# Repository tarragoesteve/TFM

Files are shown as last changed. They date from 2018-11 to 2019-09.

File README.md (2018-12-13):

# TFM
My final degree thesis is based on the construction and design of a compact remote controlled segway. Here you will find the software and the hardware needed to build one yourself when it's finished.

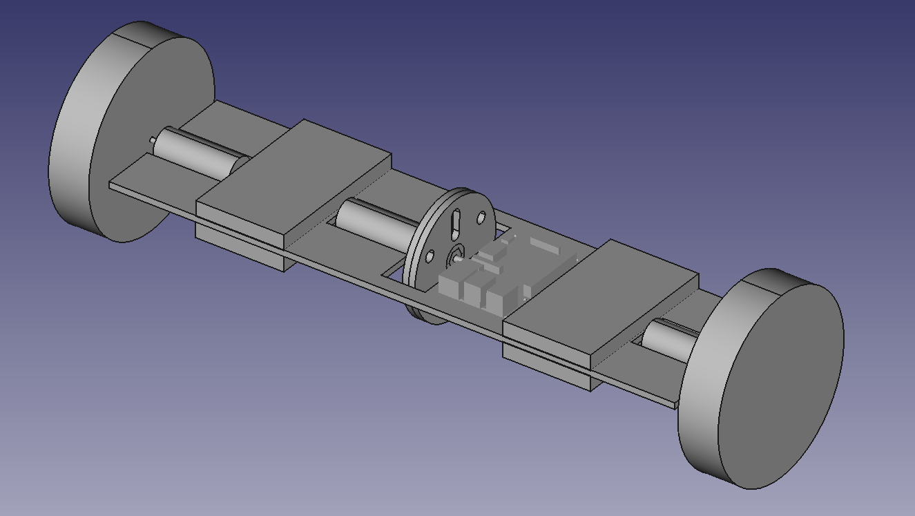
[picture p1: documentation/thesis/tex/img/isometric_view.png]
3D preview


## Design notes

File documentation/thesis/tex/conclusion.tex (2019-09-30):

\section{Conclusion}
Thinking, designing and building a prototype is a big and rewarding challenge.
There are many things that do not work as expected and you need to iterate again
and find a solution to the problem. Some examples are too much deformation in the platform,
too noisy speed measurements or 3D printed parts that we couldn't unpack.

You may see a gallery of photos
of the process in this \href{https://photos.app.goo.gl/dJozKgFnNSdTapSy6}{link} (\href{https://photos.app.goo.gl/dJozKgFnNSdTapSy6}{https://photos.app.goo.gl/dJozKgFnNSdTapSy6}).

On the other hand we came out with a model using the fundamental mechanics equations, but we are missing
some frictions and other forces that do not appear in our model. This made our robot behave a little bit
different from expected from simulations. With the flywheel mode the robot can hardly start moving and with
the pendulum mode the platform needs to turn a little to start and brake.

For a possible following iteration I would recommend much more powerful motors and a more robust structure.
The robot now is not behaving perfectly but can move around more or less as expected, as you can see in this
\href{https://youtu.be/yWOlyIL4cP0}{video} (\href{https://youtu.be/yWOlyIL4cP0}{https://youtu.be/yWOlyIL4cP0}).

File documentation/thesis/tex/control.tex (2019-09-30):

\section{Control}
So far we have analyzed our system as a continuous system.
However, we are using the Raspberry Pi to control the robot, so we will
be using digital control. It's a branch of control theory that uses
digital computers to act as system controllers.

In order to sample the position and the speed we use the rotatory encoders.
They count the number of flags so there is a constant to convert them into radians.

All our digital control was made in periodical loops. To get the speed we
divided the incremental position by the period of the loop. All the controllers
are PID controllers, each of time with different inputs, constants and outputs.

A PID controller continuously calculates an error value $e(t)$ as the difference between
a desired set point and a measured process variable and applies a
correction based on proportional, integral, and derivative terms
(denoted $K_p$, $K_i$, and $K_d$ respectively).

To adjust the controller constants in all cases we used the Ziegler-Nichols method:
\footnote{Ziegler, J.G \& Nichols, N. B. (1942). "Optimum settings for automatic controllers".
 Transactions of the ASME. 64: 759-768.}

\begin{enumerate}
    \item Set all gains to zero.
    \item Increase the $K_p$ gain until the response to a disturbance is steady oscillation.
    \item Increase the $K_d$ gain until the oscillations go away (i.e. it's critically damped).
    \item Repeat steps 2 and 3 until increasing the D gain does not stop the oscillations.
    \item Set $K_p$ and $K_d$ to the last stable values.
    \item Increase the $K_i$ gain until it brings you to the set point with no oscillations desired.
\end{enumerate}

\subsection{Position control}
The input variable is the angle we would like the motor to achieve. We sense that angle
with our rotatory encoder. The output is a PWM signal and the direction the motor has to move.

The first steep was to control the position of a peg attached to the motor.
This allowed us to move the rotor from outside and also check and adjust our encoder.
In figure \ref{fig: control peg} you can see a picture of the set up we had.

\begin{figure}[H]
    \centering
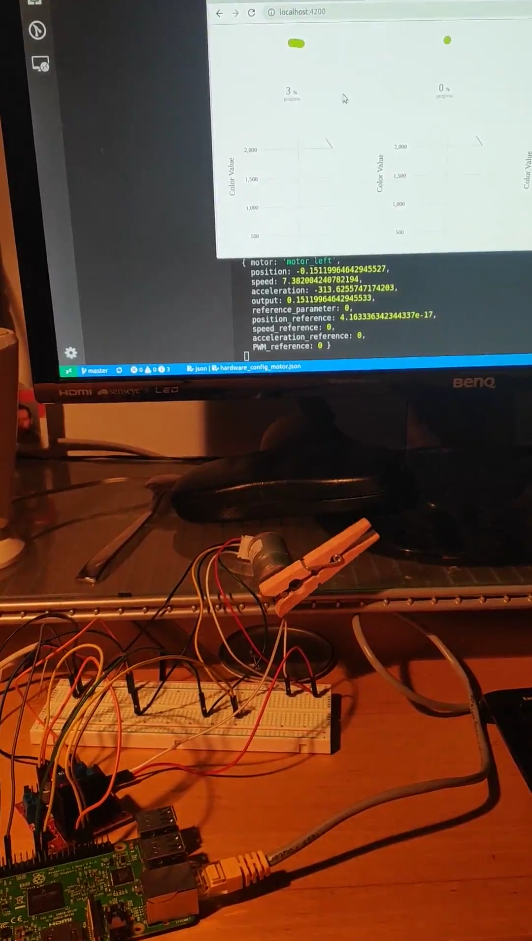
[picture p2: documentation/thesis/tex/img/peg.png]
    
    \caption{Picture of the set up to control the peg.}
    \label{fig: control peg}
\end{figure}

Once knowing the constants that worked well for our peg,
we proceed the same method with the flywheel position but having a
starting point from the peg experiment.

\subsection{Speed control}
The input variable is the desired speed. We get the real speed by dividing the incremental angle
by the period (50 ms). This leaded to noisy measurements, so we decided to apply an average filter (3 samples) to
the result.

We use the motor speed control to be able to control the direction in which the robot is moving.
We transform a two-axis joystick signal (x,y) into speed set points for the PID of the wheels
 with the following formula:
\begin{equation}
    \begin{split}
    Speed_{right} = x + y \\
    Speed_{left} = x - y    
    \end{split}
\end{equation}
\subsection{Inclination control}
In order to control the inclination of the platform we also used a PID controller.
We sense the inclination of the platform with the accelerometer, and then we compute the error
as the difference between desired inclination and sensed inclination. Them, the we feed the 

\begin{itemize}
    \item In the flywheel case we simply output this error to the flywheel PWM motor signal.
    \item In the pendulum case this output is mapped to domain from -90 degrees to 90 degrees.
    Then this signal feeds another PID controller to control the position of the pendulum. We know
    the position of the pendulum by adding the inclination we sense to the rotation of the flywheel motor.
\end{itemize}

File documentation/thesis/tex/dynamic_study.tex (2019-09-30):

\section{Rectilinear movement dynamics with $r_{flywheel}$ fixed}
This section studies the dynamics of the robot and the transition between states
to answer questions as how fast can we reach the maximum speed or how quickly can we
accelerate during a concrete period.

In order to study the dynamics of the robot we will use Lagrange mechanics.
To reduce the number of variables we will study the case of rectilinear
movement by imposing that both wheels turn at the same speed. We will also set
the radius of the free weight to $r_{flywheel}$. Note that in this analysis the
platform is not assumed to keep a fixed inclination as before, but it is allowed to rotate.

The generalized coordinates ($q$) will be:
\begin{enumerate}
	\item $\phi_{ground-wheel}$: rotation of the wheel respect the ground.
	\item $\phi_{wheel-platform}$: rotation of the platform respect the wheel.
	\item $\phi_{platform-flywheel}$: rotation of the flywheel respect the platform.
\end{enumerate}

We will use two auxiliary variables:
\begin{enumerate}
	\item $\phi_{ground-platform}=\phi_{ground-wheel}+\phi_{wheel-platform}$: rotation of the platform respect the ground.
	\item $\phi_{ground-flywheel}=\phi_{ground-platform}+\phi_{platform-flywheel}$: rotation of the flywheel respect the ground.
\end{enumerate}

The total potential energy:
\begin{equation}
	V = m_{cylinder}\cdot (r_{flywheel}-r_{flywheel-max}) \cdot cos(\phi_{ground-flywheel}) \cdot g
\end{equation}
The total kinetic energy:
\begin{equation}
	T = \frac{1}{2}\cdot[\dot{\phi}_{ground-wheel}^2\cdot I_{wheel}
		+ \dot{\phi}_{ground-platform}^2 \cdot I_{platform}
		+ \dot{\phi}_{ground-flywheel}^2\cdot I_{flywheel}
		+ \dot{\phi}_{ground-wheel}^2\cdot r_{wheel}^2\cdot m_{total}]
\end{equation}
The Lagrangian is defined as:
\begin{equation}
	L=T-V
\end{equation}
Lagrange's equation is:
\begin{equation}
	\frac{d}{dt}(\frac{\partial L}{\partial \dot{q}_j})=
	\frac{\partial L}{\partial q_j}	+ F_{j}
\end{equation}
So in our case:
\begin{equation}
	\frac{\partial L}{\partial \dot{\phi}_{ground-wheel}}=
	\dot{\phi}_{ground-wheel} \cdot I_{wheel}
	+ \dot{\phi}_{ground-platform} \cdot I_{platform}
	+ \dot{\phi}_{ground-flywheel}\cdot I_{flywheel}
	+ \dot{\phi}_{ground-wheel}\cdot r_{wheel}^2\cdot m_{total}
\end{equation}
\begin{equation}
	\frac{\partial L}{\partial \dot{\phi}_{wheel-platform}}=
	\dot{\phi}_{ground-platform} \cdot I_{platform}
	+ \dot{\phi}_{ground-flywheel}\cdot I_{flywheel}
\end{equation}
\begin{equation}
	\frac{\partial L}{\partial \dot{\phi}_{platform-flywheel}}=
	\dot{\phi}_{ground-flywheel}\cdot I_{flywheel}
\end{equation}
We define M as the following matrix:
\begin{equation}
	\begin{pmatrix}
		I_{wheel} + I_{platform} + I_{flywheel} + r_{wheel}^2 \cdot m_{total} &
		I_{platform} + I_{flywheel}                                           &
		I_{flywheel}                                                            \\
		I_{platform} + I_{flywheel}                                           &
		I_{platform} + I_{flywheel}                                           &
		I_{flywheel}                                                            \\
		I_{flywheel}                                                          &
		I_{flywheel}                                                          &
		I_{flywheel}                                                            \\
	\end{pmatrix}
\end{equation}
In matrix form and with our generalized coordinates:
\begin{equation}
	\frac{\partial L}{\partial \dot{q}} =
	M \cdot \dot{q}
\end{equation}
\begin{equation}
	\frac{d}{dt}(\frac{\partial L}{\partial \dot{q}}) = 	M \cdot \ddot{q}
\end{equation}
Let $a$ be a constant:
\begin{equation}
	a = m_{cylinder}\cdot (r_{flywheel}-r_{flywheel-max}) \cdot g
\end{equation}
\begin{equation}
	\frac{\partial L}{\partial q} = a \cdot sin(\phi_{ground-flywheel}) \cdot
	\begin{pmatrix}
		1 \\ 1 \\ 1
	\end{pmatrix}
\end{equation}
So using Lagrange's equation we get:
\begin{equation}
	\boxed{
		M \cdot \ddot{q} = a \cdot sin(\phi_{ground-flywheel}) \cdot
		\begin{pmatrix}
			1 \\ 1 \\ 1
		\end{pmatrix} + F
	}
\end{equation}
\subsection{Simulations}
In this subsection we study different policies for the generalized forces
($F$) applied to the robot in rectilinear movement case.

The robot has 2 actuators, the motors between the wheel and the platform
and the motor between the flywheel and the platform.
All motors in the systems  have a limited torque related with the
speed as you may see in Figure \ref{fig: Motor torque}.

\begin{equation}
	\boxed{
		F =
		\begin{pmatrix}
			0 \\ \tau_{wheel-platform} \\ \tau_{platform-flywheel}
		\end{pmatrix}
	}
\end{equation}

In order to compare the different policies we compare their efficiency in performing the same task:
The robot must travel 30 radians (3 meters) and stop at the end. All the parameters from 
the simulation are set equal to the values found in section \ref{sec: parameters results}.
Keep in mind that the wheel radius is 10 cm.

Here you can see a table that summarize the results:
\begin{center}
	\begin{tabular}{ |c|c|c|c|c|c|c| } 
	 \hline
	 \textbf{Experiment} & \textbf{Total time(s)} & \textbf{Time to max speed(s)} 
	 & \textbf{Max speed(rad/s)} & \textbf{Time to brake(s)}\\
	 \hline
	 \textbf{Controlling inclination} \\
	 \hline
	 Flywheel & 12,45 & 0,7 & 2,45 & 0,15\\
	 \hline
	 Pendulum & 5,59 & 2,69 & 10,36 & 2,90\\
	 \hline
	 Waitress & 8,24 & 4,12 & 5,49 & 4,12\\
	 \hline
	 \textbf{Free inclination} \\
	 \hline
	 Double flywheel & 3,9 & 1 & 8,51 & 0.27\\
	 \hline
	 Compose mechanism & 3,82 & 2,3 & 10,2 & 2,04\\
	 \hline
	\end{tabular}
\end{center}

\subsubsection{Controlling the platform inclination}
In the first two experiments we want to keep the platform in a horizontal position.
That's the reason why we force the $ \tau_{wheel-platform}$ equal to
$\tau_{platform-flywheel}$ in the experiments flywheel and pendulum.

\begin{enumerate}
	\item Flywheel
	
		The movable weight is fixed at $r_{max}$. In this experiment we consign the platform-flywheel motor to 
		output the maximum possible torque. Then the platform-wheels motors deliver
		the same torque. The platform-flywheel motor reaches in less than one second
		the maximum speed. This then limits the wheel-platform speed because no
		more torque can be applied one that point is reached.
	      \begin{figure}[H]
		      \centering
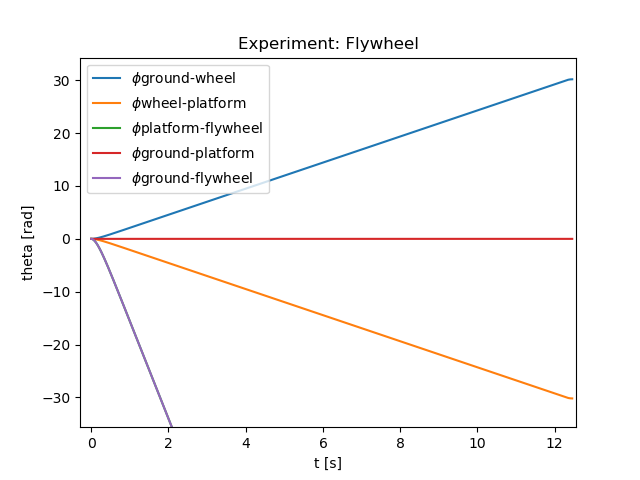
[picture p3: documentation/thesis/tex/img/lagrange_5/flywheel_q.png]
		      
		      \caption{Plot of the angles for the flywheel experiment.}
		      \label{fig:Simulation flywheel q}
	      \end{figure}

	      \begin{figure}[H]
		      \centering
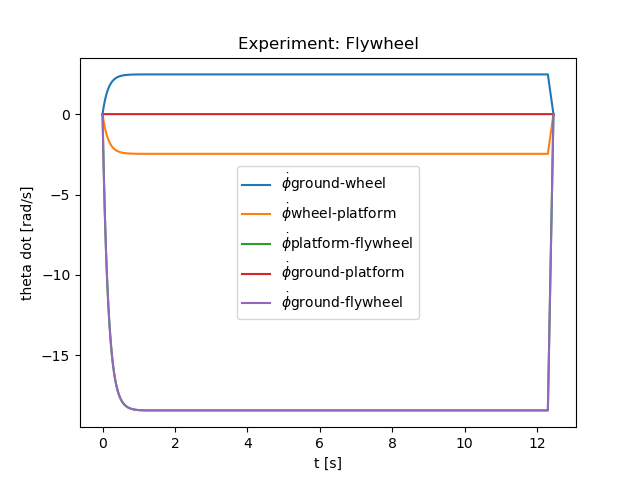
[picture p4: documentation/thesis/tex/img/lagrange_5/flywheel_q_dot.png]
		      
		      \caption{Plot of the angular velocities for the flywheel experiment.}
		      \label{fig:Simulation flywheel q dot}
	      \end{figure}
	\item Pendulum
	
		The movable weight is fixed at $r_{min}$. In this experiment we consign the platform-flywheel motor to 
		get to 90º with a PID controller. Then the platform-wheels motors deliver
		the same torque. The robot does not accelerate as fast as in the flywheel
		experiment but reaches a higher speed that allows it to travel the distance
		in less time. Note that the robot could have kept accelerating but had to
		brake before reaching the maximum speed. 
	      \
	      \begin{figure}[H]
		      \centering
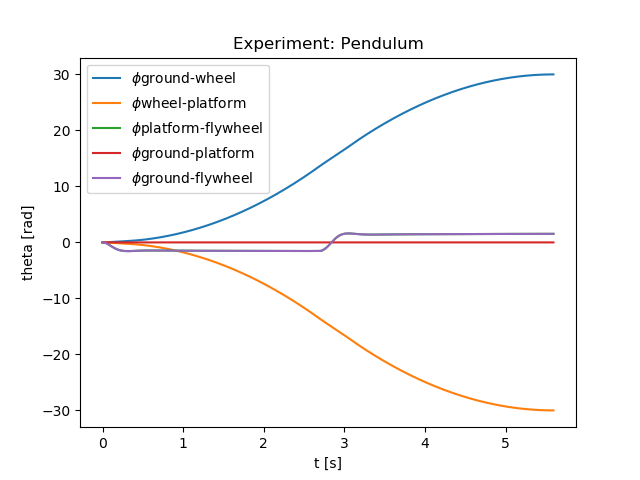
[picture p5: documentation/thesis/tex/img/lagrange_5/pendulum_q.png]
		      
		      \caption{Plot of the angles for the pendulum experiment.}
		      \label{fig:Simulation pendulum q}
	      \end{figure}

	      \begin{figure}[H]
		      \centering
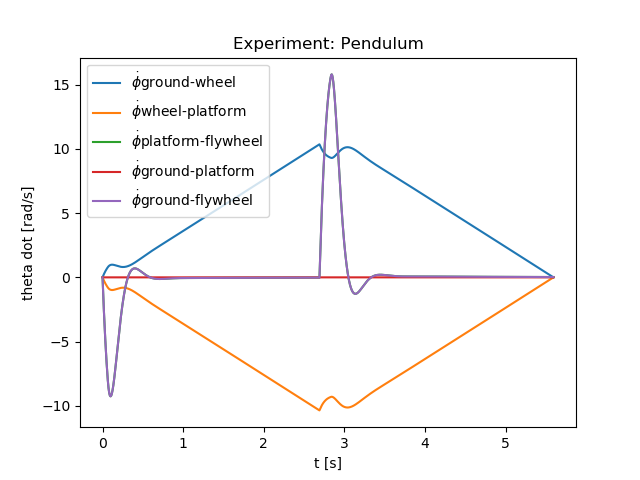
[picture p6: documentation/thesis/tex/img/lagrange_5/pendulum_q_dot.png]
		      
		      \caption{Plot of the angular velocities for the pendulum experiment.}
		      \label{fig:Simulation pendulum q dot}
	      \end{figure}
	\item Waitress
	
	The movable weight is fixed at $r_{min}$. This experiment is different from the previous two and its
	aim is to illustrate
		  how the robot could follow and inclination consign. The experiment is designed
		  the following way. A set point torque is given to the wheel-platform and the
		  flywheel-motor PID has an inclination consign too. The inclination consign is such
		  that the sum of accelerations received from and object in the platform is perpendicular
		  to the platform. 

	      \begin{figure}[H]
		      \centering
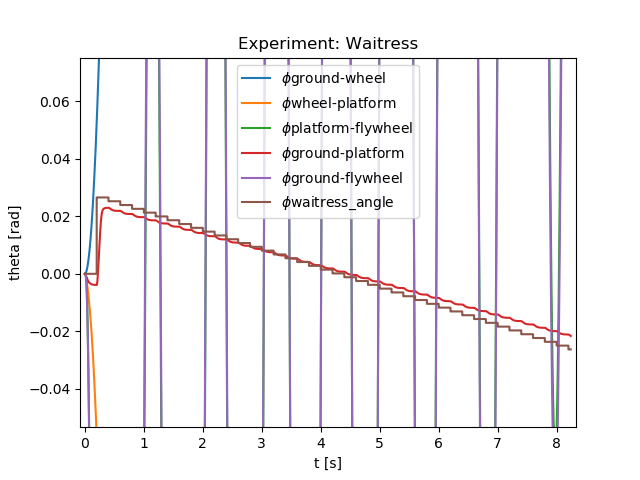
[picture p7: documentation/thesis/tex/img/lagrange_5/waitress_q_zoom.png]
		      
		      \caption{Plot of the angles for the waitress experiment.}
		      \label{fig:Simulation pendulum q}
	      \end{figure}

	      \begin{figure}[H]
		      \centering
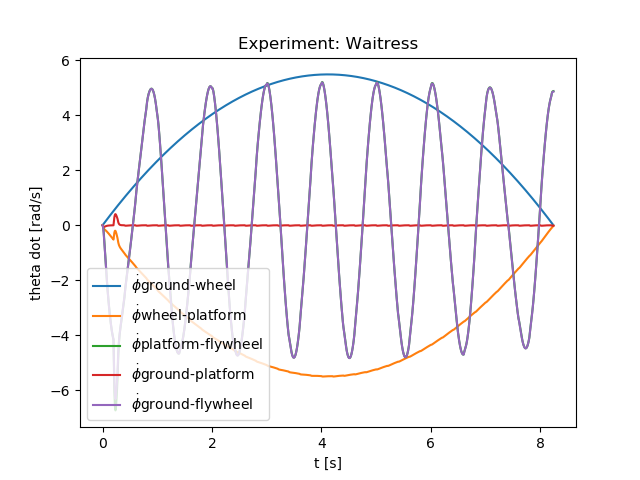
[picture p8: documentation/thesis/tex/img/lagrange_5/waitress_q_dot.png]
		      
		      \caption{Plot of the angular velocities for the waitress experiment.}
		      \label{fig:Simulation pendulum q dot}
	      \end{figure}

\end{enumerate}
\subsubsection{Letting the platform turn}
In this experiment we take advantage of the fact that the platform may not be needed
to stay horizontal in some displacement. The robot uses the platform as an
additional flywheel to help the robot accelerate and brake.
\begin{enumerate}
	\item Double Flywheel
	
	The movable weight is fixed at $r_{max}$. In this experiment we add the flywheel turn over the platform turn to 
		create more torque to accelerate our wheels. We always do the maximum possible torque with all the motors.
	      \begin{figure}[H]
		      \centering
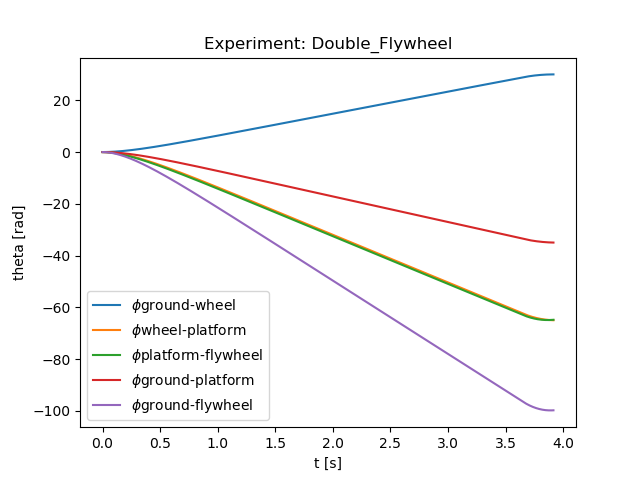
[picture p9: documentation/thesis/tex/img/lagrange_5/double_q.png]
		      
		      \caption{Plot of the angles for the double flywheel experiment.}
		      \label{fig:Simulation double q}
	      \end{figure}

	      \begin{figure}[H]
		      \centering
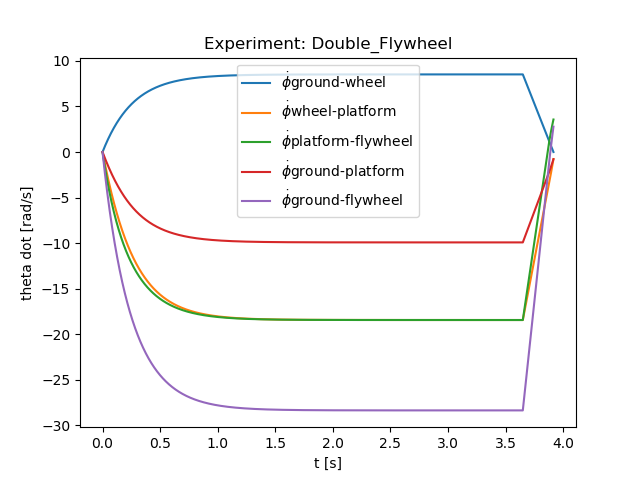
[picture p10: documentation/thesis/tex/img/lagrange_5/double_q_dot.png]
		      
		      \caption{Plot of the angular velocities for the double flywheel experiment.}
		      \label{fig:Simulation double q dot}
	      \end{figure}
	\item Compose
		  
	The movable weight is fixed at $r_{min}$. In this experiment we add the pendulum effect to the flywheel effect produced
		  by the flywheel. We do so with a PID controller for the angle ground-flywheel and making the maximum possible torque
		  with the platform-wheel motors. 
	      \begin{figure}[H]
		      \centering
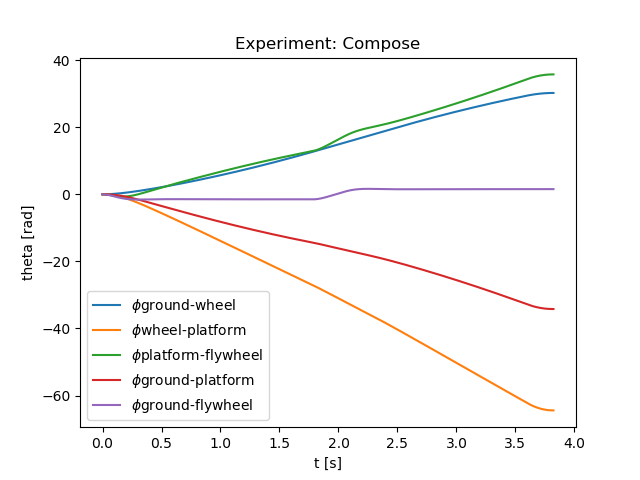
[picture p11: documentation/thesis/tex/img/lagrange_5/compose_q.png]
		      
		      \caption{Plot of the angles for the compose experiment.}
		      \label{fig:Simulation compose q}
	      \end{figure}

	      \begin{figure}[H]
		      \centering
		      
		      \caption{Plot of the angular velocities for the pendulum experiment.}
		      \label{fig:Simulation compose q dot}
	      \end{figure}
\end{enumerate}

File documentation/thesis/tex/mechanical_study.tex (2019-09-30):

\section{Mechanical analysis} \label{sec: mechanical analysis}
Once we know what we want to optimize, we need to know which is the relation with the design parameters.
In this section we will analyze and understand the key dynamics of our robot, so we can choose
the design parameters based on performance indicators. All the analysis is made
supposing the inclination of the platform is maintained fixed. As parameters, we have the width of the
flywheel masses $w$, the number of masses $N$, the radius of the flywheel $r_{flywheel}$, and
the radius of the wheels $r_{wheel}$.

\subsection{Inclination control}
In order to keep the inclination of the platform at a certain angle $\phi$ 
we must be able to compensate all the torque being applied to the platform.

\[\ddot{\phi}\cdot I_{platform} = \tau_{platform} \]

Assuming that the platform is well-balanced (the center of masses is located
at the rotation axis by our design restriction) and neglecting the torque generated
by the friction
with air, the sum of all the torques in the motor axis applied to the platform
is equal to the sum of the torque applied by the motors:

\[\tau_{platform} = \sum \tau_{motors}\]

The torque that the motors deliver to the wheels and to the flywheel create
a reaction in the platform in the opposite direction.

\[\tau_{platform} = -\tau_{motor-right-wheel} -\tau_{motor-left-wheel} -\tau_{motor-flywheel} \]

If we want keep the inclination $\phi$, we must be able to cancel $\tau_{platform}$.
Observe that the angular acceleration $\ddot{\phi}$ of the platform is linearly 
dependent with the torque it receives. 
\begin{equation} \label{eq:control equation}
\begin{split}
0 = -\tau_{motor-right-wheel} -\tau_{motor-left-wheel} -\tau_{motor-flywheel} \Rightarrow \\
\tau_{motor-right-wheel} +\tau_{motor-left-wheel} = -\tau_{motor-flywheel}
\end{split}
\end{equation}
In other words, we must overpass the torque of the wheels with the torque of the flywheel
if we want to control the inclination.

\subsection{Wheels torque}
The wheel torque we can induce is limited by the motor specifications.
Note that the maximum torque of the motor is a function of velocity and in particular 
at max speed the torque is zero. See figure \ref{fig: Motor torque} to see the plot of this function.

\[\tau_{motor-wheel} (\omega_{wheel}) \]

\begin{figure}
	\centering
    \begin{tikzpicture}
        %Axis
            \draw[->,thin] (center.center) -- (0,3.5) node[above] {$\tau_{motor}$};
            \draw[->,thin] (center.center) -- (3.5,0) node[right] {$\omega$};
        %Function
            \node (stall) at (0,3) [left]{stall torque};
            \node (maximum) at (3,0) [below]{maximum speed};
            \draw[-] (0,3) -- (3,0);
        \end{tikzpicture}
    \caption{Motor torque.}
	\label{fig: Motor torque}
\end{figure}

We assume that the wheels just roll and do no slip.
The robot is pushed by the wheels that make a force $F_{friction}$ against the ground in the contact point. See figure \ref{fig:Wheel force diagram}.

We can express the torque at the center of the wheel as:
\[\tau_{motor-wheel} + F_{friction} \cdot r_{wheel} = I_{wheel} 
\cdot \dot{\omega}_{wheel} \]
\begin{equation} \label{wheel torque equation}
\tau_{motor-wheel} = I_{wheel} \cdot \dot{w}_{wheel} - F_{friction} \cdot r_{wheel}
\end{equation}
\begin{figure}[ht]
	\centering
	\begin{tikzpicture}
        \path[rotate=30] node (center) at (2,2) {};
        \draw (center) circle (2);
        \draw[rotate=30] (0,0) -- (4,0);
        \draw[dashed] (0,0) -- (4,0);
        \path node[above] (right) at ([shift=({2,0})]center) {};
        \draw[<->] (center.center) -- (right.center)  node[below, midway] {$r_{wheel}$};;
    %Arcs
        \draw[rotate=30, ->] (4.5,2) arc (0:30:2.5) node[above]{$\omega_{wheel}$};
        \draw[rotate=30, ->, thick] (2.5,2) arc (0:60:.5) node[above]{$\tau_{motor-wheel}$};

        \draw[->] (1,0) arc (0:30:1) node[right]{$\alpha$};
    %Forces
        \draw[rotate=30,->,thick] (2,0) -- (3.5,0) node[above]{$F_{friction}$};
        \draw[rotate=30,->,thick] (2,0) -- (2,1) node[above]{$N$};
        \path node[above] (below) at ([shift=({0,-1})]center) {};
    
        \draw[->,thick] (center.center) -- (below.center) node[below]{$m\cdot g$};
        \draw[rotate=30,->,thick] (center.center) -- (1,2) node[below]{$F_{platform}$};
    \end{tikzpicture}
	\caption{Wheel force diagram.}
	\label{fig:Wheel force diagram}
\end{figure}

\subsection{Flywheel torque}
\begin{figure}
	\centering
    \begin{tikzpicture}
        %Circle
            \path node (center) at (0,0) {};
            \draw (center) circle (3);
        %Arcs
            \draw[->] (0,3.5) arc (90:120:3.5) node[above, midway]{$\theta$};
        %Movable mass
            \draw[rotate=120,fill=gray] (1.5,0) circle (.9) node (moving) [draw,circle]{};
        %Guide
            \draw[dashed,rotate=120] (.9,0) -- (2.1,0);
        %Other masses
            \foreach \i in {2}
            {
                \draw[rotate=60-60* \i,fill=gray] (3-.9,0) circle (.9) node[draw,circle]{};
            }
        %Radius
            \draw[<->] (0,0) -- (moving.center) node[near end, below] {$r$};
            \draw[rotate=-60,<->] (0,0) -- (2.1,0) node[midway, above] {$r_{max}$};
        %Axis
            \draw[->,thin] (center.center) -- (0,3.5) node[above] {$z$};
            \draw[->,thin] (center.center) -- (3.5,0) node[right] {$y$};
        %Motor torque
        \draw[->, thick] (0.5,0) arc (0:60:.5) node[right]{$\tau_{motor-flywheel}$};    
    \end{tikzpicture}
            \caption{Flywheel diagram for $N$ = 2}
	\label{fig:Flywheel force diagram}
\end{figure}

The flywheel torque we can induce is also limited by the motor specifications. 

Assuming a general configuration of the flywheel where the moving mass is at distance $r$ from 
the axis and angle $\theta$, see figure \ref{fig:Flywheel force diagram}, we formulate its torque the following way:
\[
    \tau_{motor-flywheel} + m_{cylinder} \cdot g \cdot (r - r_{max}) \cdot \sin{\theta} = \ddot{\theta}\cdot I_{flywheel}(r)  
\]
\begin{equation}\label{eq: flywheel torque equation}    
    \tau_{motor-flywheel} = \ddot{\theta}\cdot I_{flywheel}(r) + m_{cylinder} \cdot g \cdot (r_{max} - r) \cdot \sin{\theta}  
\end{equation}
Note that in equation \ref{eq: flywheel torque equation} the two terms correspond to the two 
two mechanisms: acceleration of the flywheel and position of the pendulum.

\subsection{Maximum speed, acceleration and terrain inclination}
In this subsection we would like to study the maximum speed and acceleration the robot may
obtain in straight direction and the maximum terrain inclination it can stand on $\alpha$.

We will assume both wheels turn at the same speed, have the same $F_{friction}$ and the same $\tau_{wheel}$:
\[ \omega_{wheel-left} = \omega_{wheel-right} = \omega_{wheel} \]
\begin{figure}
	\centering
	\begin{tikzpicture}
        \path[rotate=30] node (center) at (2,2) {};
        \draw (center) circle (2);
        \draw[rotate=30] (0,0) -- (4,0);
        \draw[dashed] (0,0) -- (4,0);
        \path node[above] (right) at ([shift=({2,0})]center) {};
        \draw[<->] (center.center) -- (right.center)  node[below, midway] {$r_{wheel}$};;
    %Arcs
        \draw[rotate=30, ->] (4.5,2) arc (0:30:2.5) node[above]{$\omega_{wheel}$};
        \draw[rotate=30, ->, thick] (2.5,2) arc (0:60:.5) node[above]{$\tau_{motor-wheel}$};

        \draw[->] (1,0) arc (0:30:1) node[right]{$\alpha$};
        \draw[rotate=30,<-] (2,.5) arc (270:240:1.5) node[below, midway]{$\alpha$};
    %Forces
        \draw[rotate=30,->,thick] (2,0) -- (3.5,0) node[above]{$F_{friction}$};
        \draw[rotate=30,->,thick] (2,0) -- (2,1) node[above]{$N$};
        \path node[above] (below) at ([shift=({0,-1})]center) {};
    
        \draw[->,thick] (center.center) -- (below.center) node[below]{$m\cdot g$};
        \draw[rotate=30,->,thick] (center.center) -- (1,2) node[below]{$F_{platform}$};
    %Axis
        \draw[->,thin][rotate=30] (center.center) -- (2,5) node[above] {$z$};
        \draw[->,thin][rotate=30] (center.center) -- (5,2) node[right] {$y$};
        \draw[dashed][rotate=30] (center.center) -- (2,1);

    \end{tikzpicture}
    \caption{Wheel forward force diagram.}
    \label{fig:Wheel forward force diagram}
\end{figure}

Applying Newton's first law in the y-axis of figure \ref{fig:Wheel forward force diagram}:
\[\ddot{y}\cdot m_{total} = 2 \cdot F_{friction} - m_{total} \cdot g \cdot sin(\alpha)\]
Substituting $F_{friction}$ taking in to account equation \ref{wheel torque equation}:
\[\ddot{y}\cdot m_{total} = 2 \cdot \frac{I_{wheel} \cdot \dot{w}_{wheel}-\tau_{motor-wheel}}{r_{wheel}} - m_{total} \cdot g \cdot sin(\alpha)\]
Using equation \ref{eq:control equation}:
\begin{equation}\label{eq of acceleration}
    \Rightarrow  \ddot{y}\cdot m_{total} = \frac{2\cdot I_{wheel} \cdot \dot{w}_{wheel}}{r_{wheel}} + \frac{\tau_{motor-flywheel}}{r_{wheel}} - m_{total} \cdot g \cdot sin(\alpha)
\end{equation}
We will now study different cases to better understand this equation.

\subsubsection{Speed and acceleration with no terrain inclination ($\alpha = 0$)}
The objective here is to obtain the maximum speed and acceleration we can get starting from rest in a plain surface.

The equation we get by substituting $\alpha = 0$ in equation \ref{eq of acceleration}:
\[\ddot{y}\cdot m_{total} = \frac{\tau_{motor-flywheel}}{r_{wheel}} +\frac{2\cdot I_{wheel} \cdot  \dot{w}_{wheel}}{r_{wheel}}\]

Substituting equation \ref{eq: flywheel torque equation}:
\begin{equation}\label{eq: no inclintation}
    \ddot{y}\cdot m_{total} = \frac{\ddot{\theta}\cdot I_{flywheel}(r) +
    m_{cylinder} \cdot  g \cdot  (r_{max} - r) \cdot  \sin{\theta}}{r_{wheel}} +\frac{2\cdot I_{wheel} \cdot  \dot{\omega}_{wheel}}{r_{wheel}}
\end{equation}

We will now split the study in two cases:
\begin{enumerate}
    \item \textbf{Flywheel case:} $r$ is fixed to $r = r_{max}$ 
    
    Then:  
    \[\ddot{y}\cdot m_{total} = - \frac{\ddot{\theta}\cdot I_{flywheel}(r_{max})}
    {r_{wheel}} + \frac{2\cdot I_{wheel} \cdot  \dot{\omega}_{wheel}}{r_{wheel}}\]

    Taking in to account the following relation:
    \begin{equation} \label{eq: angular velocity}
        -\omega_{wheel} \cdot  r_{wheel} = \dot{y} \Rightarrow  -\dot{\omega}_{wheel} \cdot  r_{wheel} = \ddot{y}  
    \end{equation}

    Substituting in equation \ref{eq: no inclintation}:
    \[-\dot{\omega}_{wheel} \cdot  r_{wheel}\cdot m_{total} = \frac{\ddot{\theta}\cdot I_{flywheel}}
    {r_{wheel}} + \frac{2\cdot I_{wheel} \cdot  \dot{\omega}_{wheel}}{r_{wheel}} \]

    \[-\dot{\omega}_{wheel} \cdot (r_{wheel}\cdot m_{total} +  \frac{2\cdot I_{wheel} }{r_{wheel}}) = 
    \frac{\ddot{\theta}\cdot I_{flywheel}}{r_{wheel}}\]

    We now define R as a non dimensional constant being the quotient between $\dot{w}_{wheel}$ and $-\ddot{\theta}$.

    \begin{equation}\label{eq: R definition}
        R = \frac{\dot{\omega}_{wheel}}{-\ddot{\theta}} = 
    \frac{I_{flywheel}}
    {r_{wheel}^2\cdot m_{total} +  2\cdot I_{wheel}}
    \end{equation}

    The moments of inertia are:
    \[I_{wheel} \approx \frac{1}{2} \cdot m_{wheel} \cdot  r_{wheel}^2\]
    \[I_{flywheel} \approx N \cdot  m_{cylinder} \cdot  r_{max}^2\]

    Substituting those in equation \ref{eq: R definition} we get:
    \[R \approx
    \frac{ N \cdot  m_{cylinder} \cdot  r_{max}^2}
    {r_{wheel}^2\cdot m_{total} +  2\cdot I_{wheel}} < 1 \] 

    We can see that R will always be smaller than 1 because $N \cdot  m_{cylinder} < m_{total} $ and $r_{max} < r_{wheel}$.
    
    This means that the maximum acceleration of the wheels will be limited by the acceleration of the flywheel. The same is true for the speed.

    In  order to get the forward acceleration we can use equation \ref{eq: angular velocity}
    \[\ddot{y} = -\dot{\omega}_{wheel} \cdot  r_{wheel} = R \cdot  \ddot{\theta} \cdot  r_{wheel}\]
    And using equation \ref{eq: flywheel torque equation} we get that the maximum is:

    \[\tau_{motor} (\omega) = \ddot{\theta}\cdot I_{flywheel}(r) \Rightarrow \ddot{\theta} = \frac{\tau_{motor} (\dot{\theta})}{I_{flywheel}(r)} \]

    \[\ddot{y}_{max} = R \cdot  \frac{\tau_{motor} (\dot{\theta})}{I_{flywheel}(r)} \cdot  r_{wheel}\]

    \[\Rightarrow \ddot{y}_{max} =     \frac{I_{flywheel}}
    {r_{wheel}^2\cdot m_{total} +  2\cdot I_{wheel}}  \cdot  \frac{\tau_{motor} (\dot{\theta})}{I_{flywheel}(r)} \cdot  r_{wheel}\]
    \begin{equation}        
        \boxed{\ddot{y}_{max} = \frac{\tau_{motor}(\dot{\theta})\cdot r_{wheel} }
        {r_{wheel}^2\cdot m_{total} +  2\cdot I_{wheel}}}
        \label{maximum acceleration flywheel}
    \end{equation}
    In order to compute the maximum speed we assume that the initial conditions are $\dot{\theta} = 0$ and 
    $\omega_{wheel}=0$

    \[\omega_{wheel-max} = \int_{t=0}^{t=t_{max}} \dot{\omega}_{wheel} \cdot  dt\]

    Now we will proceed to do a change of variables in the integral.

    \[
    \frac{\partial \dot{\theta}}{\partial t} = \ddot{\theta} \Rightarrow dt = \frac{d\dot{\theta}}{\ddot{\theta}}
    \]
    
    \[\omega_{wheel-max} = \int_{\dot{\theta}=0}^{\dot{\theta}=\dot{\theta}_{max}} \frac{\dot{\omega}_{wheel}}{\ddot{\theta}} \cdot  d\dot{\theta} = 
    \int_{\dot{\theta}=0}^{\dot{\theta}=\dot{\theta}_{max}} -R \cdot  d\dot{\theta} = - R \cdot  \dot{\theta}_{max}
    \]
    \begin{equation}
        \boxed{\dot{y}_{max} = r_{wheel} \cdot  R \cdot  \dot{\theta}_{max}}
        \label{Maximum speed flywheel}
    \end{equation}
    And $\dot{\theta}_{max}$ is a limitation imposed by the motor specifications. Note that this is the maximum speed
    we can get using the flywheel system starting from rest.

    \item \textbf{Pendulum:} $\dot{\theta} = 0$, and $r$ is fixed to $r = r_{min}$
    
    Using equation \ref{eq: no inclintation} and $\ddot{\theta} = 0$
    \[\ddot{y}\cdot m_{total} = \frac{m_{cylinder} \cdot  g \cdot  (r_{max} - r_{min}) \cdot  \sin{\theta}}{r_{wheel}} +\frac{2\cdot I_{wheel} \cdot  \dot{w}_{wheel}}{r_{wheel}}\]
    Multiplying by $r_{wheel}$ both sides of the equation we get:
    \[\ddot{y}\cdot m_{total} \cdot  r_{wheel} = m_{cylinder} \cdot  g \cdot  (r_{max}-r_{min}) \cdot  \sin{\theta} + 2\cdot I_{wheel} \cdot  \dot{w}_{wheel}\]
    And using $\dot{w}_{wheel} = -\frac{\ddot{y}}{r_{wheel}}$
    \[\ddot{y}\cdot m_{total} \cdot  r_{wheel} + 2\cdot  I_{wheel} \cdot  \frac{\ddot{y}}{r_{wheel}} = m_{cylinder} \cdot  g \cdot  (r_{max}-r) \cdot  \sin{\theta} \]
    With some manipulation:
    \[\ddot{y}  = \frac{m_{cylinder} \cdot  g \cdot  (r_{max}-r_{min}) \cdot  \sin{\theta}}{m_{total} \cdot  r_{wheel} + \frac{2\cdot I_{wheel}}{r_{wheel}} }  \]
    Which is maximum when $\sin{\theta}=1$
    \begin{equation}
        \boxed{ \ddot{y}_{max}  = \frac{m_{cylinder} \cdot  g \cdot  (r_{max}-r_{min}) \cdot}{m_{total} \cdot  r_{wheel} + \frac{2\cdot I_{wheel}}{r_{wheel}} } }
        \label{maximum acceleration pendulum}
    \end{equation}
    Since the maximum acceleration obtained is constant, the speed could increase without limit. To get a meaningful estimation of the maximum speed,
    we will take into account the air friction that becomes more and more important as the speed increases.
    
    \[F_{drag} = \frac{1}{2}\cdot \rho\cdot C_D \cdot  A \cdot  \dot{y}^2 \]

    Adding this term to equation \ref{eq of acceleration} we get:
    \[  \ddot{y}\cdot m_{total} = \frac{2\cdot I_{wheel} \cdot  \dot{w}_{wheel}}{r_{wheel}} + \frac{\tau_{motor-flywheel}}{r_{wheel}} - m_{total} \cdot  g \cdot  sin(\alpha) - F_{drag} \]
    And making $\ddot{y} = 0$ and $\alpha = 0$.
    \[  F_{drag} = \frac{\tau_{motor-flywheel}}{r_{wheel}}\]

    \[\frac{1}{2}\cdot \rho\cdot C_D \cdot  A \cdot  \dot{y}^2 = m_{cylinder} \cdot  g \cdot  (r_{max} - r_{min})\cdot sin(\theta) / r_{wheel} \]
    The maximum $\dot{y}$ is then obtained when $\theta=\frac{\pi}{2}$:
    \begin{equation*}
        \dot{y}_{max} = \sqrt{\frac{2\cdot m_{cylinder} \cdot  g \cdot  (r_{max} - r_{min})}{\rho\cdot C_D \cdot  A \cdot  r_{wheel}} }
    \end{equation*}

    We will pick $C_D=1$, $\rho=1.2 kg/m^3$ and $A=0.01 m^2$ for our computations.

    Also, note that the speed is also limited by maximum speed a motor can get
    $\dot{\theta}_{max}$.
    \begin{equation}
        \boxed{\dot{y}_{max} = min(\dot{\theta}_{max}\cdot r_{wheel}, \sqrt{\frac{2\cdot m_{cylinder} \cdot  g \cdot  (r_{max} - r_{min})}{\rho\cdot C_D \cdot  A \cdot  r_{wheel}} })}
        \label{maximum speed pendulum}
    \end{equation}

\end{enumerate}
\subsubsection{Terrain inclination ($\alpha > 0$)}
The goal of this subsection is to study which is the maximum terrain inclination $\alpha_{max}$ 
on which the robot can stay, standing still without rolling down.

Substituting $\ddot{y}=0$ and $\dot{\omega}_{wheel} = 0$ in equation \ref{eq of acceleration}
\[0 = \frac{\tau_{motor-flywheel}}{r_{wheel}} - m_{total} \cdot  g \cdot  sin(\alpha)\]
\[m_{total} \cdot  g \cdot  sin(\alpha) = \frac{\tau_{motor-flywheel}}{r_{wheel}} \]
\[sin(\alpha) = min(1,\frac{\tau_{motor-flywheel}}{m_{total} \cdot  g \cdot  r_{wheel}}) \]

Substituting equation \ref{eq: flywheel torque equation}
\[sin(\alpha) = min(1,\frac{\ddot{\theta}\cdot I_{flywheel}(r) + m_{cylinder} \cdot  g \cdot  (r_{max} - r) \cdot  \sin{\theta}}{m_{total} \cdot  g \cdot  r_{wheel}}) \]

We are going to distinguish the same two cases as in the previous section:
\begin{enumerate}
    \item Flywheel case: $r$ is fixed to $r = r_{max}$
    The maximum inclination at a certain moment:
    \begin{equation}\label{Maximum angle using flywheel system}
        \boxed{sin(\alpha_{max}) = min(1,\frac{\ddot{\theta}\cdot I_{flywheel}}{m_{total} \cdot  g \cdot  r_{wheel}}) = min(1,\frac{\tau_{motor-flywheel}(\dot{\theta})}{m_{total} \cdot  g \cdot  r_{wheel}})}
    \end{equation}

    This angle doesn't give us a lot of information because it may not be fulfilled in a 
    permanent state.
    
    \item Pendulum: $\dot{\theta} = 0$, and $r$ is fixed to $r = r_{min}$
    \[sin(\alpha) = \frac{min(\tau_{motor-flywheel},m_{cylinder} \cdot  g \cdot  (r_{max} - r_{min}) \cdot  \sin{\theta})}{m_{total} \cdot  g \cdot  r_{wheel}} \]
    Which is maximum when $\sin{\theta} = 1$
    \begin{equation}\label{Maximum angle using pendulum system}
        \boxed{sin(\alpha_{max}) = \frac{min(\tau_{motor-flywheel},m_{cylinder} \cdot  g \cdot  (r_{max} - r_{min}))}{m_{total} \cdot  g \cdot  r_{wheel}}}
    \end{equation}
    Note that the $sin(\alpha_{max})$ will not be more than 1.
\end{enumerate}

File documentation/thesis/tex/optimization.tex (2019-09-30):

\section{Optimization Setup}
We want to size our design before building our prototype. We would like it to be optimal, so 
we have set up the requirements and the cost function we want to optimize.

\subsection{Restrictions}
The restrictions are a list of inequalities that our system has to fulfill.
The first restriction is due to the initial design requirements. Finally, the other three are 
somehow arbitrary but will help us to reduce the size of the robot.
\begin{enumerate}
\item We will place our flywheel in a hole on our robot. We don't want to touch the ground
in any configuration so:
\begin{figure}[ht]
	\centering
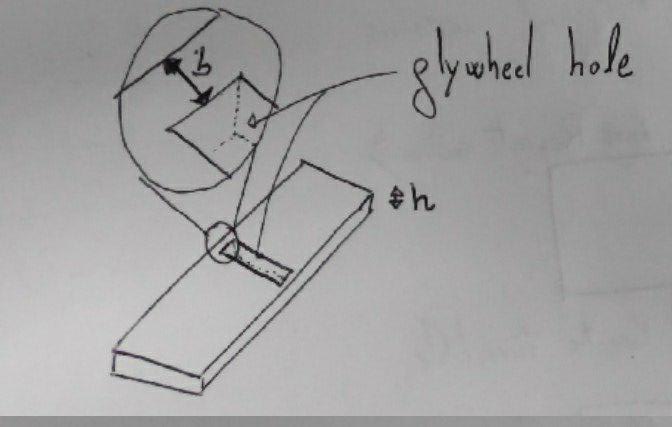
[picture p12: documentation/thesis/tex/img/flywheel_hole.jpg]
	
	\caption{Flywheel hole diagram}
	\label{fig:Flywheel hole diagram}
\end{figure}
\[r_{wheel}> \sqrt{(r_{flywheel} + b)^2+(\frac{h}{2})^2}\]
\item Being able  to insert the robot in to a wheel of diameter 0.5 m so:
\begin{figure}[ht]
	\centering
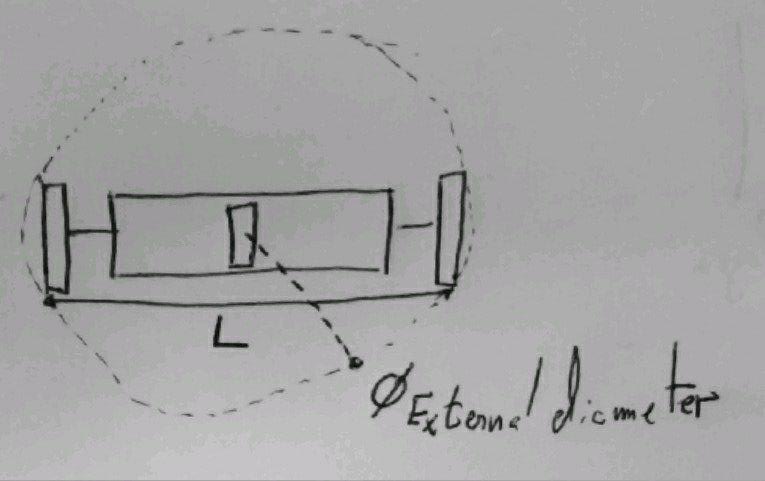
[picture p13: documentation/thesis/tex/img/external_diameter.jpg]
	
	\caption{External diameter diagram}
	\label{fig:External diameter diagram}
\end{figure}
\[0.25 m > \sqrt{r_{wheel}^2 + L^2/4}\]
\item We can place all electronic the devices:
\[L > 0.3m + w \]
\item Maximum weight of the robot: 5 kg
\end{enumerate}

\subsection{Requirements}
We would like our robot to reach some mechanical specifications. These are related to mechanical equations
that we will develop in the next section. They refer to the max speed, acceleration and terrain inclination the robot may achieve
while controlling its platform inclination. We have divided our specifications in two blocks
according to the two mechanisms.

\textbf{Flywheel mode}
\begin{enumerate}
	\item $\dot{y}_{max}$ (equation \ref{Maximum speed flywheel}) $> 0.1m/s$.
	\item $\ddot{y}_{max}$ (equation \ref{maximum acceleration flywheel}) $> 1m/s^2$.
	\item $sin(\alpha_{max})$ (equation \ref{Maximum angle using flywheel system}) $>0.16$.
\end{enumerate}

\textbf{Pendulum mode}
\begin{enumerate}
	\item $\dot{y}_{max}$ (equation \ref{maximum speed pendulum}) $>1m/s$.
	\item $\ddot{y}_{max}$ (equation \ref{maximum acceleration pendulum}) $>0.1m/s^2$.
	\item $sin(\alpha_{max})$ (equation \ref{Maximum angle using pendulum system}) $> 0.02$.
\end{enumerate}

\subsection{Cost function}
In addition to fulfilling the previous inequalities, we will adjust our design parameters [w (width of the
cylinders), N(number of cylinders), r wheel and r flywheel] to
minimize a cost function. 

We will maximize the maximum sinus in the pendulum mode 
(equation \ref{Maximum angle using pendulum system}) because
it gives the robot the capacity to deliver force in a permanent state.

And we will also maximize the square of the max speed the robot can achieve
in flywheel mode (equation \ref{Maximum speed flywheel}) because it is
proportional to the energy the robot can deliver using the flywheel at a certain moment.

Both equations try to maximize different modes so the robot we have a compromise between the two of them. 

\begin{equation}
	cost(r_{flywheel},r_{wheel},w,N) = - sin(\alpha_{max})_{pendulum} -\dot{y}^2_{max-flywheel}
	\label{eq: cost}
\end{equation}
In the next section we will find out what are the values 
of these equations with the construction parameters. 
%For reference these terms are equal to:
%\begin{equation*}
%	m_{cylinder} = \rho * w * \pi * (\frac{r_{flywheel}}{3})^2
%\end{equation*}
%\begin{equation*}
%	sin(\alpha_{max})_{pendulum} = \frac{m_{cylinder} \cdot  (r_{max} - r_{min})}{m_{total} \cdot r_{wheel}} = \frac{m_{cylinder} \cdot  (\frac{r_{flywheel}}{3})}{(m_{rest} + N \cdot m_{cylinder})\cdot r_{wheel}} 	
%\end{equation*}
%\begin{equation*}
%	\dot{y}_{max} = r_{wheel} \cdot  R \cdot  \dot{\theta}_{max} =r_{wheel} \cdot  \frac{ N \cdot  m_{cylinder} \cdot  (\frac{2\cdot r_{flywheel}}{3})^2}
%    {r_{wheel}^2\cdot (m_{rest} + N \cdot m_{cylinder}) +  2\cdot I_{wheel}} \cdot  \dot{\theta}_{max}
%\end{equation*}

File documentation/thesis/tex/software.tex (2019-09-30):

\section{Software Design}
We designed the software as modular and reusable as we could, having in mind
possible future expansions of the project.
The code is divided in three main blocks: user interface (UI), planner and controller.

The UI sends the user commands to the planner, and then the planner translates these commands to
position or speed set points and sends it to the controller. Then the controller runs the control algorithms
and reports back the sensors measurements.

The reality is that the planner workload now is low but in the future it may need to compute harder problems,
as image processing, artificial intelligence or multi-robot coordination.

These three blocks are now running in three different computers but can run in any configuration if needed.

You can find all the code in the GitHub repository \url{https://github.com/tarragoesteve/TFM} under the 
software folder.

\subsection{User Interface}
The user interface is a 3 column layout, the left column is for the left motor, the central column for the platform inclination and the flywheel motor
and the right one for the right motor. As you can see in figure \ref{fig: UI}, each column has three elements,
a round progress bar to indicate the set point, a radio selection to select which parameter you wish to command and a plat
of the sensor readings.
\begin{figure}[H]
    \centering
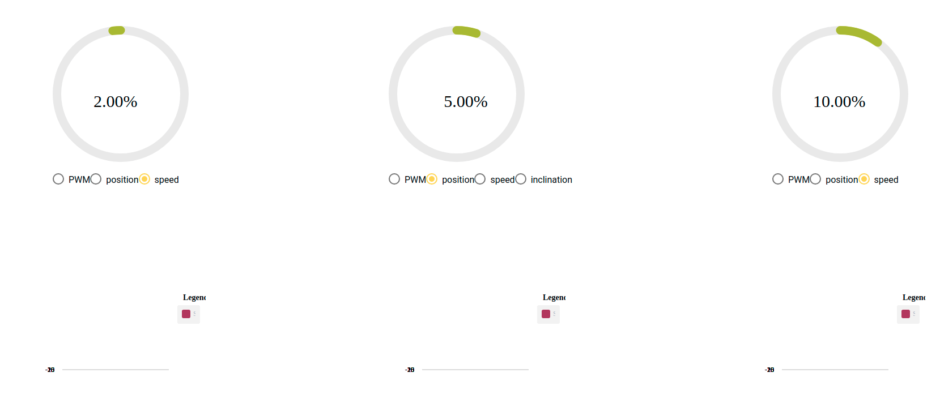
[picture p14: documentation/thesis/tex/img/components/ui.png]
    
    \caption{Screen shoot of the UI.}
    \label{fig: UI}
\end{figure}
The user interface can be controlled by the keyboard or by a joy-stick connected to the computer. In our case
we used a PS4 remote controller connected via bluetooth to the computer.

The whole interface was programmed with Angular, a TypeScript framework designed to code user interfaces.
It is organized in modules and packages that one can install, as the round progress bar. An Angular Server is 
running in the client machine that can connect to the interface via website.

\subsection{Planner}
The planner main job is to receive and send messages through sockets to the UI and the controller. Sockets is a method to communicate
different processes across the internet with very low latency. The planner is working on a server with a public IP
so the other computers know where they have to exchange the information even if the UI or the Controller changes its IP.

The planner is now working mainly as a communication module but could be to plan robot moves based on the user input or
any algorithm.

\subsection{Controller}
The controller is running on the Raspberry Pi. It has a main file (controller.js) that reads
a configuration file (config.json) and creates instances of the components described on the configuration file.
Once all components are created, it starts different threads for each of the components to run their loops.

The different components we have: accelerometer, led, motor and stabilizer. Also, we have two auxiliary classes that are
not components: PID and average filter. All the components that rely on hardware are using C++ code to optimize
the code. This code is wrapped in TypeScript classes to make an easier integration of sockets and JSON files.

\subsubsection{LED}
This was the first components that we made to test the software.
It has a GPIO pin as a parameter that it's where we connect the LED.
Then the main loop changes the state of the LED each 500 ms making it blink.
\subsubsection{Motor}
The motor class has the encoder code incorporated. The encoder uses the interruptions to update the position of the motor.
And the loop of this component is using the PID controller to generate an output based on the reference and the position readings.
It then applies this output value to the 3 output pins of the motor (1 PWM and 2 for direction of the H Bridge).
\subsubsection{Accelerometer}
The accelerometer component provides a method to get the inclination of the platform via an I2C communication with
the MPU-6050.
\subsubsection{Stabilizer}
The stabilizer component is made up of two other components: a motor and an accelerometer. In its loop it calculates
the inclination error and uses the motor to send a pendulum consign or a PWM signal (depending on the mode).

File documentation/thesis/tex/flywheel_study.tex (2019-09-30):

\section{Flywheel brake study}

The problem with the flywheel method is that, when it reaches the maximum speed, the motor cannot apply torque. 
This section aims to study a possible way to break the flywheel without applying torque to the platform.
The idea is combining both methods: we will leave the moving weight free.

The initial hypothesis was: If we let weight move, when it is going upward will have a larger radius than 
when is going downward and will produce an average external torque against 
the movement of the flywheel. From an energetic point of view we are transforming the rotation energy of
the flywheel in to translation of the free cylinder and then releasing it trough collisions.

\subsection{System of differential equations}
To simplify the experiment we will assume that the platform inclination is constant and that the motor is not
producing any torque to the platform.

As described in figure \ref{fig:Flywheel force diagram} we will use two variables to describe
the flywheel position: $r$ and $\theta$.

Using equation \ref{eq: flywheel torque equation}:
\[\tau_{motor-flywheel} = \ddot{\theta}*I_{flywheel}(r) + m_{cylinder} * g * 
(r_{max} - r) * \sin({\theta})  \]
\begin{figure}[H]
	\centering
	\begin{tikzpicture}
        %Center
            \path node (center) at (0,0) {};
        %Arcs
            \draw[->] (0,3.5) arc (90:120:3.5) node[above, midway]{$\theta$};
        %Movable mass
            \draw[rotate=120,fill=gray] (1.5,0) circle (.9) node (moving) [draw,circle]{};
        %Guide
            \draw[dashed,rotate=120] (.9,0) -- (2.1,0);
        %Radius
            \draw[<->] (0,0) -- (moving.center) node[near end, below] {$r$};
		%Forces
			\draw[->, very thick] (moving.center) -- ([shift=({0,-1.5})]moving.center) node[below]{$m*g$};
			\draw[->, very thick, rotate=120] (1.5,0) -- (2.7,0) node[above]{$m*r*\dot{\theta}^2$};
		%Axis
            \draw[->,thin] (center.center) -- (0,3.5) node[above] {$z$};
            \draw[->,thin] (center.center) -- (3.5,0) node[right] {$y$};
    \end{tikzpicture}
	\caption{Cylinder force diagram.}
	\label{fig:Cylinder force diagram}
\end{figure}

As seen in figure \ref{fig:Cylinder force diagram}, we can deduce Newton's equation for the distance from the cylinder to the center $r$. Note that we are adding the centrifugal force term due to the non-inertial frame.
\[\ddot{r} * m = -m * g * cos(\theta) + m * r * \dot{\theta}^2 \]
\[\ddot{r} = -g * cos(\theta) + r * \dot{\theta}^2 \]
The variables we will be using for our ODE system are: $r$,$\dot{r}$,$\theta$,$\dot{\theta}$.

Note that we impose $\tau_{flywheel} = 0$ so the motor is not applying any torque.

\[
\begin{cases}
    \dot{r} = \dot{r}\\
    \ddot{r} = -g * cos(\theta) + r * \dot{\theta}^2\\
    \dot{\theta} = \dot{\theta}\\
    \ddot{\theta} = \frac{m_{cylinder} * g * (r - r_{max}) * \sin{\theta}}{I_{flywheel}(r)} \\    
\end{cases}
\]

Our initial conditions will be the free cylinder mass lying on the bottom of the flywheel and the flywheel turning at a speed $\theta_0$:
\[
    \begin{cases}
        r = r_{max} \\
        \dot{r} = 0\\
        \theta = \pi\\
        \dot{\theta} = \theta_0\\
    \end{cases}
\]
We will use a Poincar\'e map to simulate the bounce with the end of the guides at $r=r_{min}$ and $r=r_{max}$. At each bounce we will reduce its kinetic energy by a percentage $bounce\_percentage$.

\subsection{Results}
The parameters of the simulation where:
\[
\begin{cases}
	r_{flywheel} = 8cm \\
	r_{wheel} = 9cm \\
	w = 7 cm \\
	\dot{\theta}_0 = 4.2 \pi rad/s \\
	bounce\_percentage = 0.0 (totally\_inelastic) \\	
\end{cases}	
\]
\begin{figure}[H]
	\centering
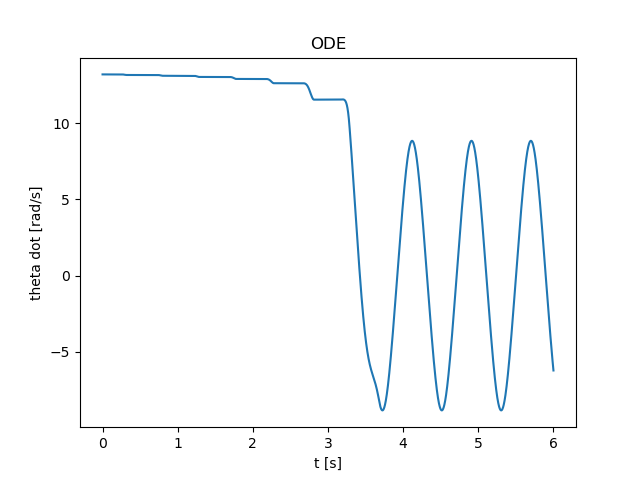
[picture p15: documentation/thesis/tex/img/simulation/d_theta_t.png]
	
	\caption{How the variable $\dot{\theta}$ evolve over time}
	\label{fig:d theta t diagram}
\end{figure}
As we can see in figure \ref{fig:d theta t diagram} the flywheel is braking until it becomes a pendulum and starts oscillating.

\begin{figure}[H]
	\centering
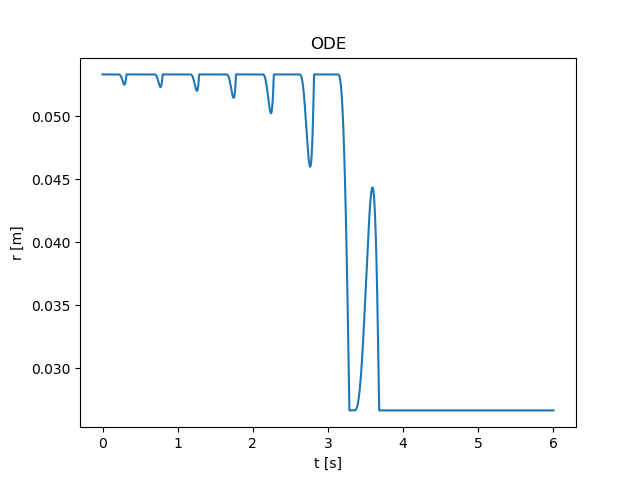
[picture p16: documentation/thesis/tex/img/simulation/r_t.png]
	
	\caption{How the variable $r$ evolves over time}
	\label{fig:r t diagram}
\end{figure}
In the first laps the cylinder is almost always at the maximum value of r, but as the
speed decreases each lap the value of $r$ decreases until it hits the $r_{min}$.
In other words, at the beginning is operating as a flywheel but then thanks to the
collisions it becomes a pendulum.

\begin{figure}[H]
	\centering
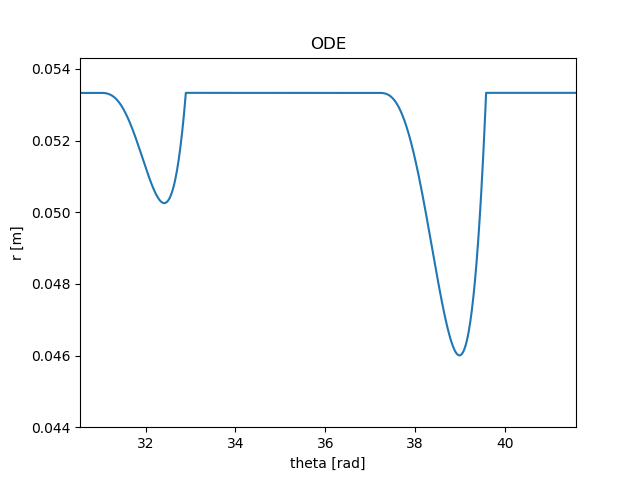
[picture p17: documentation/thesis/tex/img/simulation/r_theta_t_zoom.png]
	
	\caption{How the variable $r$ evolve over $\theta$ zoomed}
	\label{fig:r theta zoom}
\end{figure}
In image \ref{fig:r theta zoom} we can appreciate that the r decreases slower than what it increases.

\begin{figure}[H]
	\centering
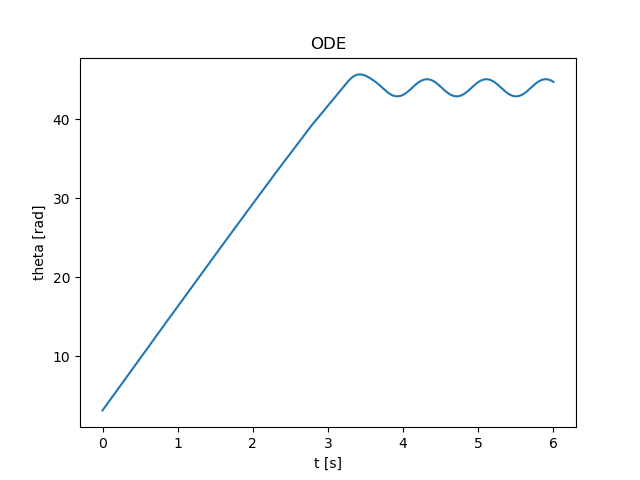
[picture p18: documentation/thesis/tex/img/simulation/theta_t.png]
	
	\caption{How the variable $\theta$ evolves over time.}
	\label{fig:theta t diagram}
\end{figure}

\begin{figure}[H]
	\centering
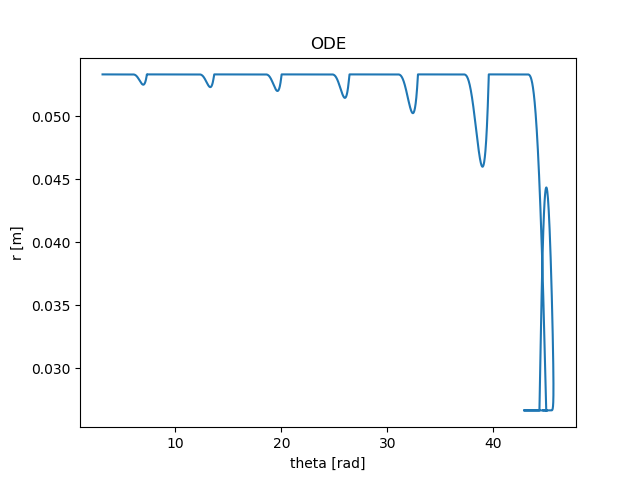
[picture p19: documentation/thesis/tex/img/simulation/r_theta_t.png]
	
	\caption{How the variable $r$ evolves over $\theta$.}
	\label{fig:r theta}
\end{figure}

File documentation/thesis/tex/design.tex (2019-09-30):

\section{Initial design considerations}
The first thing we decided was the number of actuators.
Most of segway robots include two motors for the motion control, but
we added a third on in order to control the inclination.
So we ended up with three motors in total because we want to control
three degrees of freedom (inclination and speed of both wheels).

In order to control the inclination of the platform we needed to produce
an external torque to the platform. We considered three methods: accelerating
a flywheel, holding a pendulum in a non-vertical position and air friction
with a fan. We discarded the last one due to the high speeds we needed to obtain
a reasonable torque on the platform.

Both methods have strengths in different situations, so we decided to build a mixed
piece that could combine both. The flywheel mode allows to deliver the maximum torque from
the beginning but fails to deliver a continuous torque due to the motor achieving max speed.
In the other hand the pendulum allows the system to apply a constant amount of torque over time.

We took two more restriction in our design. The first one symmetry along the motors/inclination
axis in order to have an equilibrium in all possible inclinations without the need of external forces.
We also took in consideration that some experiments may start produce arbitrary rotations of the platform,
so none of the configurations should touch the ground to avoid crashes. Figure \ref{fig:Side render view} illustrates this last restriction.

The design of the robot was done with the 3D design software \href{https://www.freecadweb.org/}{Free-cad} and 
most of the parts were 3D printed. 3D printing has also its own restrictions, for example not being able to print
parts bigger than 25 cm. All part files are uploaded to the GitHub repository \url{https://github.com/tarragoesteve/TFM}
under the hardware folder. So anyone can build this robot.

You can see the main views of an initial design on Figure \ref{fig:Isometric render view},
\ref{fig:Front render view}, \ref{fig:Top render view} and \ref{fig:Side render view}.

\begin{figure}
	\centering
	
	\caption{Isometric render view}
	\label{fig:Isometric render view}
\end{figure}
\begin{figure}
	\centering
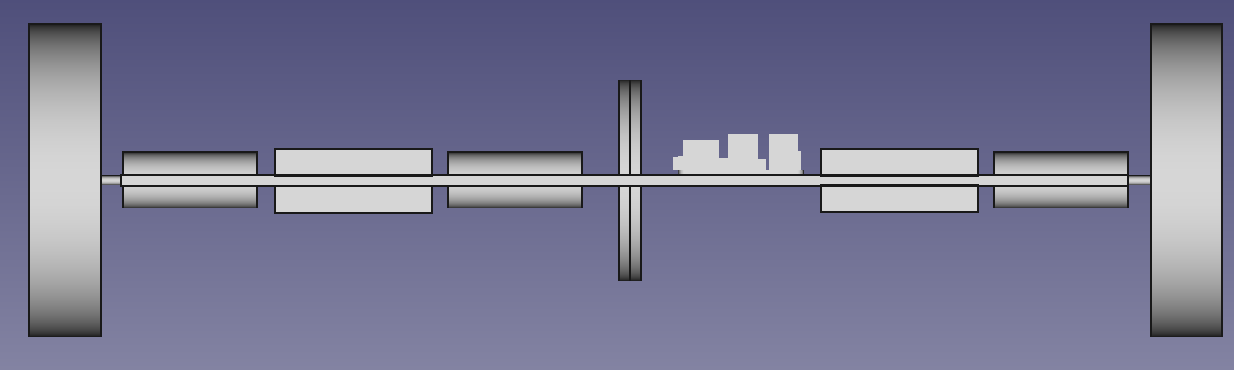
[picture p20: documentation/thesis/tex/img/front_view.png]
	
	\caption{Front render view}
	\label{fig:Front render view}
\end{figure}
\begin{figure}
	\centering
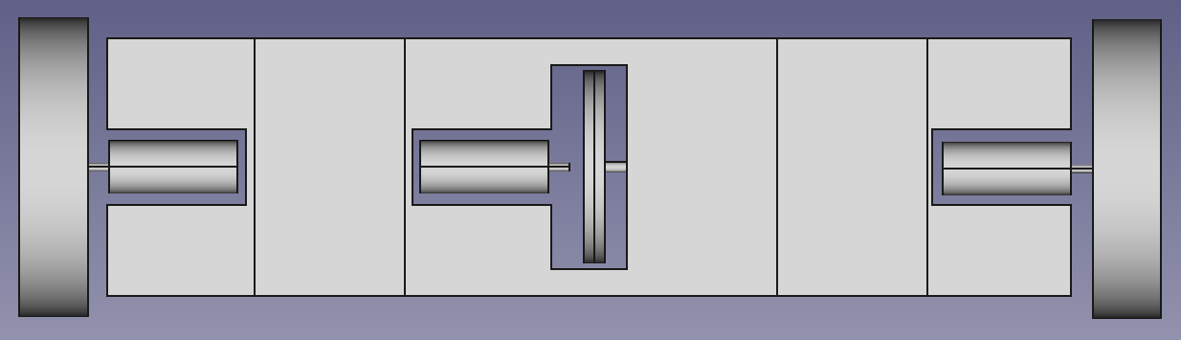
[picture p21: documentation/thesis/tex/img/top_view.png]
	
	\caption{Top render view.}
	\label{fig:Top render view}
\end{figure}
\begin{figure}
	\centering
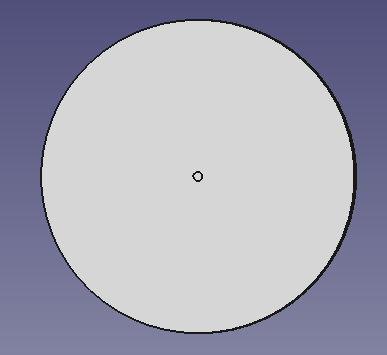
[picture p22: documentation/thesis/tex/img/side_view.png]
	
	\caption{Side render view.}
	\label{fig:Side render view}
\end{figure}

\subsection{Flywheel design} \label{sec: flywheel design}
\begin{figure}
	\centering
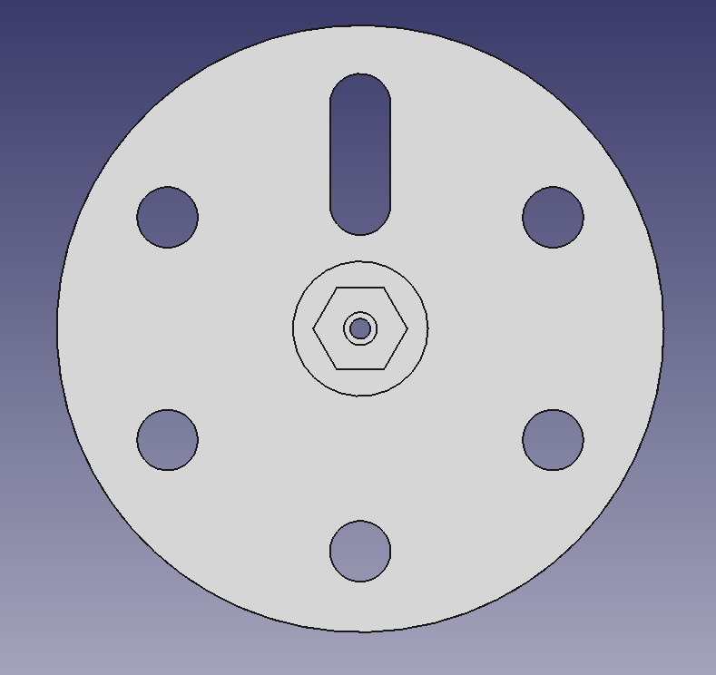
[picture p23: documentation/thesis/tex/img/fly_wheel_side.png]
	
	\caption{Flywheel side render view.}
	\label{fig:Fly wheel side render view}
\end{figure}

To control the inclination of the body two strategies are taken into account.
Creating torque by a pendulum or accelerating the flywheel.
In order to experiment with both of them we designed a part to allow
both configurations by placing weights in different spots, see figure
\ref{fig:Fly wheel side render view}.

In order to create a configuration with maximum pendulum torque
we have done the following computation. We denote the pendulum
torque by $\tau$, consider the masses are cylinders of mass $m_{cylinder}$
with radius $r_{cylinder}$ and width $w$ and the radius of the flywheel is $r_{flywheel}$.
We want to place all $N$ masses at the same distance of the center of the flywheel ($r_{max}$) in
a regular polygon except for one mass that will be at $r_{min}$. See figure \ref{fig:Fly wheel side render view}.

Each mass weights:
\[ m_{cylinder} = \rho \cdot w \cdot \pi \cdot r_{cylinder}^2 \]

We neglect the mass of the flywheel structure versus the mass of the cylinders. All
the gravitational torque is created by the cylinder masses and all of them are compensated
with the opposite weight except for the two masses with different radius.

One of the weights can be placed along a track. The distance to the center will
vary from $r_{min} = r_{cylinder} + r_{motor-axis} \approx r_{cylinder} $ to $r_{max} = r_{flywheel} - r_{cylinder}$.

The maximum torque takes place when these two masses are aligned horizontal with respect to the ground and the movable weight is at distance $r_{min}$ from the center.

\[ \tau _{max} (r_{cylinder}) =  m_{cylinder} \cdot g \cdot r_{max} -  m_{cylinder} \cdot g \cdot r_{min} =
	m_{cylinder}\cdot g \cdot (r_{flywheel} - 2 \cdot r_{cylinder}) \]

In order find the radius $r_c$ that maximizes $\tau$ we first compute the derivative:
\[\frac{\partial \tau _{max} (r_{cylinder})}{\partial r_c} = g \cdot(\frac{\partial m}{\partial r_c} \cdot (r_f - 2 \cdot r_c) -  m_{cylinder} \cdot 2)\]

\[ \frac{\partial  m_{cylinder}}{\partial r_{cylinder}} = 2 \cdot \rho \cdot w \cdot \pi \cdot  r_{cylinder}\]

And make it zero to find the maximum:

\[\frac{\partial \tau _{max} (r_{cylinder})}{\partial r_{cylinder}} = 0\]

Substituting and simplifying we get:

\[\frac{\partial m}{\partial r_{cylinder}} \cdot (r_{flywheel} - 2 \cdot r_{cylinder}) =
	m_{cylinder} \cdot 2 \Rightarrow 2 \cdot \rho \cdot w \cdot \pi \cdot  r_{cylinder}\ \cdot (r_{flywheel} - 2 \cdot r_{cylinder}) = \rho \cdot w \cdot \pi \cdot r_c^2 \cdot 2 \]

\[ \Rightarrow r_c\ \cdot (r_{flywheel} - 2 \cdot r_{cylinder}) =  r_{cylinder}^2
	\Rightarrow (r_{flywheel} - 2 \cdot r_{cylinder}) =  r_{cylinder}
	\Rightarrow \boxed{r_f = 3 \cdot r_{cylinder}}\]

The circumradius $R$ from the center of a regular polygon to one of the vertices is related to the side length $s$ by:

\begin{center}
	\begin{tabular}{ c  c }
		\(\displaystyle R=\frac {s}{2\cdot \sin{\frac {\pi} {n}}} \)
		 &
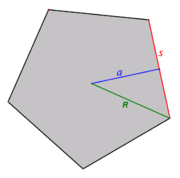
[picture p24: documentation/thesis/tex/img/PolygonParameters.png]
		
	\end{tabular}
\end{center}

In our case:
\[ R = r_{flywheel} - r_{cylinder}; \]
\[ s = 2 \cdot r_{cylinder}\]

Substituting in the circumradius equation we get n = 6, so we will use up to 6 masses in our flywheel.
We will have a variable number of masses $N$ that we will be able to add to
the flywheel as shown in the following table:
\begin{center}
	\begin{tabular}{c | c | c | c }
		2 & 3 & 4 & 6 \\
		\begin{tikzpicture}[scale=0.5]
			%Circle
			\path node (center) at (0,0) {};
			\draw (center) circle (3);
			%Movable mass
			\draw[rotate=120,fill=gray] (1.5,0) circle (.9) node (moving) [draw,circle]{};
			%Guide
			\draw[dashed,rotate=120] (.9,0) -- (2.1,0);
			%Other masses
			\foreach \i in {2}
				{
					\draw[rotate=60-60*\i,fill=gray] (3-.9,0) circle (.9) node[draw,circle]{};
				}
		\end{tikzpicture}

		  &
		\begin{tikzpicture}[scale=0.5]
			%Circle
			\path node (center) at (0,0) {};
			\draw (center) circle (3);
			%Movable mass
			\draw[rotate=120,fill=gray] (1.5,0) circle (.9) node (moving) [draw,circle]{};
			%Guide
			\draw[dashed,rotate=120] (.9,0) -- (2.1,0);
			%Other masses
			\foreach \i in {1,3}
				{
					\draw[rotate=60-60*\i,fill=gray] (3-.9,0) circle (.9) node[draw,circle]{};
				}
		\end{tikzpicture}
		  &
		\begin{tikzpicture}[scale=0.5]
			%Circle
			\path node (center) at (0,0) {};
			\draw (center) circle (3);
			%Movable mass
			\draw[rotate=120,fill=gray] (1.5,0) circle (.9) node (moving) [draw,circle]{};
			%Guide
			\draw[dashed,rotate=120] (.9,0) -- (2.1,0);
			%Other masses
			\foreach \i in {1,2,4}
				{
					\draw[rotate=60-60*\i,fill=gray] (3-.9,0) circle (.9) node[draw,circle]{};
				}
		\end{tikzpicture}
		  &

		\begin{tikzpicture}[scale=0.5]
			%Circle
			\path node (center) at (0,0) {};
			\draw (center) circle (3);
			%Movable mass
			\draw[rotate=120,fill=gray] (1.5,0) circle (.9) node (moving) [draw,circle]{};
			%Guide
			\draw[dashed,rotate=120] (.9,0) -- (2.1,0);
			%Other masses
			\foreach \i in {1,2,3,4,6}
				{
					\draw[rotate=60-60*\i,fill=gray] (3-.9,0) circle (.9) node[draw,circle]{};
				}
		\end{tikzpicture}
		\\
	\end{tabular}
\end{center}

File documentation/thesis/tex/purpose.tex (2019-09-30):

\section{Introduction}
In the IRI lab we have two segway robots, Tibi and Dabo shown in figure
\ref{fig:Picture of Tibi and Dabo}. Both of them move the same way.
They must incline their body to command the wheels' rotation. We will get deeper
in why these phenomena happens in section \ref{sec: mechanical analysis}.

This movement restriction may cause some problems when trying to avoid obstacles,
as for example going through low roof path. Another limitation is the
acceleration that the robot can achieve which is directly related with the inclination
that it's limited to 90 degrees in the best case. Also, the amount of uphill
is limited with an additional problem: the safety system stops the robot if 
it detects something near it (in this case the ground).

So we decided to build a prototype of segway robot that could solve this problem by 
controlling its inclination independently. The chosen robot is inspired in a
\textit{segway hoverboard}, similar to the one appearing in Figure \ref{fig:Picture of a commercial 
segway hover-board}. The two wheels are controlled with classic control algorithms and the
inclination of the central body is controlled with a flywheel mechanism that we will
discuss in section \ref{sec: flywheel design}.
\begin{figure}
	\centering
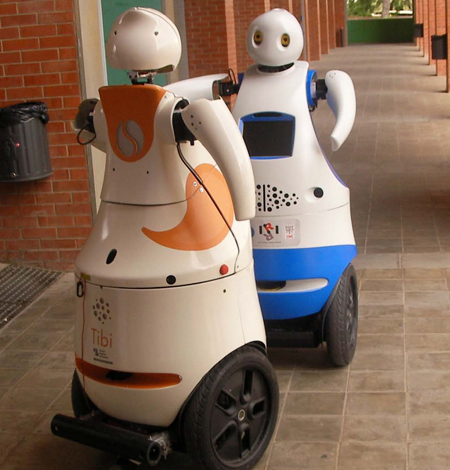
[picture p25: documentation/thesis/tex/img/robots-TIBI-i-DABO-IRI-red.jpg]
	
	\caption{Picture of Tibi and Dabo, \textit{two segway robots} }
	\label{fig:Picture of Tibi and Dabo}
\end{figure}

\begin{figure}
	\centering
	
	\caption{Picture of a commercial \textit{segway hoverboard} }
	\label{fig:Picture of a commercial segway hover-board}
\end{figure}

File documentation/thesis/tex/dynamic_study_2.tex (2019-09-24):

\section{Rectilinear movement with $r_{flywheel}$ free}
In this section we have developed the Lagrange Mechanics for the system with
one mass of the flywheel being free (i.e. Movable along a rail).

The generalized coordinates ($q$) will be:
\begin{enumerate}
	\item $\phi_{ground-wheel}$: rotation of the wheel respect the ground.
	\item $\phi_{wheel-platform}$: rotation of the platform respect the wheel.
	\item $\phi_{platform-flywheel}$: rotation of the flywheel respect the platform.
	\item $r$: distance from the center of the flywheel to the free cylinder.
\end{enumerate}

We will use two auxiliary variables:
\begin{enumerate}
	\item $\phi_{ground-platform}=\phi_{ground-wheel}+\phi_{wheel-platform}$: rotation of the platform respect the ground.
	\item $\phi_{ground-flywheel}=\phi_{ground-platform}+\phi_{platform-flywheel}$: rotation of the flywheel respect the ground.
\end{enumerate}

The total potential energy:
\begin{equation}
	V = m_{cylinder}\cdot (r-r_{flywheel-max}) \cdot cos(\phi_{ground-flywheel}) \cdot g
\end{equation}

The total kinetic energy:
\begin{multline}
	T = \frac{1}{2}\cdot[\dot{\phi}_{ground-wheel}^2\cdot I_{wheel}
		+ \dot{\phi}_{ground-platform}^2 \cdot I_{platform}
		+ \dot{\phi}_{ground-flywheel}^2\cdot I_{flywheel}(r)\\
		+ \dot{\phi}_{ground-wheel}^2\cdot r_{wheel}^2\cdot m_{total}
		+ \dot{r}^2\cdot m_{cylinder}]
\end{multline}

The Lagrangian is defined as:
\begin{equation}
	L=T-V
\end{equation}

Lagrange's equation is:
\begin{equation}
	\frac{d}{dt}(\frac{\partial L}{\partial \dot{q}_j})=
	\frac{\partial L}{\partial q_j}	+ F_{j}
\end{equation}

So in our case:
\begin{multline}
	\frac{\partial L}{\partial \dot{\phi}_{ground-wheel}}=
	\dot{\phi}_{ground-wheel} \cdot I_{wheel}
	+ \dot{\phi}_{ground-platform} \cdot I_{platform}\\
	+ \dot{\phi}_{ground-flywheel}\cdot I_{flywheel}(r)
	+ \dot{\phi}_{ground-wheel}\cdot r_{wheel}^2\cdot m_{total}
\end{multline}

\begin{equation}
	\frac{\partial L}{\partial \dot{\phi}_{wheel-platform}}=
	\dot{\phi}_{ground-platform} \cdot I_{platform}
	+ \dot{\phi}_{ground-flywheel}\cdot I_{flywheel}(r)
\end{equation}

\begin{equation}
	\frac{\partial L}{\partial \dot{\phi}_{platform-flywheel}}=
	\dot{\phi}_{ground-flywheel}\cdot I_{flywheel}(r)
\end{equation}

\begin{equation}
	\frac{\partial L}{\partial \dot{r}}=
	\dot{r}\cdot m_{cylinder}
\end{equation}

We define M as the following matrix:
\begin{equation}
	\begin{pmatrix}
		I_{wheel} + I_{platform} + I_{flywheel}(r) + r_{wheel}^2 \cdot m_{total} &
		I_{platform} + I_{flywheel}(r)                                           &
		I_{flywheel}(r)                                                          &
		0                                                                          \\
		I_{platform} + I_{flywheel}(r)                                           &
		I_{platform} + I_{flywheel}(r)                                           &
		I_{flywheel}(r)                                                          &
		0                                                                          \\
		I_{flywheel}(r)                                                          &
		I_{flywheel}(r)                                                          &
		I_{flywheel}(r)                                                          &
		0                                                                          \\
		0                                                                        &
		0                                                                        &
		0                                                                        &
		m_{cylinder}                                                               \\
	\end{pmatrix}
\end{equation}

In matrix form and with our generalized coordinates:
\begin{equation}
	\frac{\partial L}{\partial \dot{q}} =
	M \cdot \dot{q}
\end{equation}

\begin{equation}
	\frac{d}{dt}(\frac{\partial L}{\partial \dot{q}}) =
	M \cdot \ddot{q} + \dot{M} \cdot \dot{q}
\end{equation}

Let's recall the definition of $I_{flywheel}(r)$
\begin{equation}
	I_{flywheel}(r)= m_{cylinder} \cdot r^2 + C
\end{equation}

Compute the derivative
\begin{equation}
	\dot{I}_{flywheel}(r)= 2 \cdot m_{cylinder} \cdot r \cdot \dot{r}
\end{equation}

We compute $\dot{M}$ as the following matrix:
\begin{equation}
	\dot{M}=
	\dot{I}_{flywheel}(r) \cdot
	\begin{pmatrix}
		1 &
		1 &
		1 &
		0   \\
		1 &
		1 &
		1 &
		0   \\
		1 &
		1 &
		1 &
		0   \\
		0 &
		0 &
		0 &
		0   \\
	\end{pmatrix}
\end{equation}

Let $a$ be::
\begin{equation}
	\frac{\partial L}{\partial q_{1..3}} = a = m_{cylinder}\cdot (r-r_{flywheel-max}) \cdot g \cdot sin(\phi_{ground-flywheel})
\end{equation}

Let $b$ be:
\begin{equation}
	\frac{\partial L}{\partial r} = b = \cdot m_{cylinder} \cdot r  \cdot \dot{\phi}_{ground-flywheel}^2  - m_{cylinder}\cdot g \cdot cos(\phi_{ground-flywheel})
\end{equation}

\begin{equation}
	\frac{\partial L}{\partial q} = \begin{pmatrix}
		a \\ a \\ a \\ b
	\end{pmatrix}
\end{equation}

So using Lagrange's equation we get:
\begin{equation}
	\boxed{
		M \cdot \ddot{q} + \dot{M} \cdot \dot{q}=
		\begin{pmatrix}
			a \\ a \\ a \\ b
		\end{pmatrix}
		+ F
	}
\end{equation}

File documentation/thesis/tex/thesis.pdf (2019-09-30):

## Universitat Politècnica de Catalunya

## Facultat de Matemàtiques i Estadística

## Master in Advanced Mathematics and Mathematical Engineering

# Master’s thesis

# A Remotely-driven Hoverboard With Platform Leaning Control

## Esteve Tarragó

## Supervised by Advisor: Enric Celaya, Tutor: Mercè Ollè

## September, 2019

I would first like to thank my thesis advisor Prof. Enric Celaya. Enric was always open whenever I ran into a trouble spot or had a question about my research or writing. He consistently allowed this thesis to be my own work, but steered me in the right the direction whenever he thought I needed it.
I would also like to thank Prof. Lluís Ros who was also advising me through the first steps of the design and always gave constructive feedback.
Also this project wouldn’t have been possible without my lab co-workers. I would like to highlight three of them: Iñigo Moreno, Sergi Hernandez and Patrick Grosch. They taught me all kinds of stuff and I am very grateful for their time.
This research opportunity was possible thanks to IRI (Institut de Robtica i Informtica Industrial). They facilitated me a workstation, material and a fantastic workshop where to build my robot.

## Abstract

This thesis is centered around the design, construction and control of a remotely controlled hoverboard. The main challenge of this project is the study of the leaning control of the hoverboard platform and the restrictions it induces.
Nowadays, segways are a popular way of human transportation and there also exist segway robots. Both, human-driven and autonomous segway robots have their speed determined by their inclination. (e.i. If you wish to go forward in a segway, then you should put your weight in the same direction). So in these systems the inclination is not a degree of freedom but a necessary condition from moving. Unblocking this degree of freedom may help two-wheel robots perform new tasks as measurements, taking images or samples from other inclinations, avoiding obstacles, etc.
We have studied different mechanisms to control the leaning of the platform while allowing the movement of the robot. Then, we studied the dynamics of our system in order to determine its dimensions and create an optimal design accordingly. We have also run simulations with different policies to see how our system would evolve.
Finally, we built and programmed our robot so it can be remotely operated from anywhere.

Keywords

Dynamic, System, Control, Design

# Contents

1 Introduction | 4
2 Initial design considerations | 6
3 Optimization Setup | 10
4 Mechanical analysis | 12
5 Optimization Results | 19
6 Rectilinear movement dynamics with rflywheel fixed | 24
7 Flywheel brake study | 32
8 Rectilinear movement with rflywheel free | 36
9 Components | 38

10 Control | 45
11 Software Design | 48
12 Conclusion | 50

Leaning Control


Figure 1: Picture of Tibi and Dabo, two segway robots

# 1. Introduction

In the IRI lab we have two segway robots, Tibi and Dabo shown in figure 1. Both of them move the same way. They must incline their body to command the wheels’ rotation. We will get deeper in why these phenomena happens in section 4.
This movement restriction may cause some problems when trying to avoid obstacles, as for example going through low roof path. Another limitation is the acceleration that the robot can achieve which is directly related with the inclination that it’s limited to 90 degrees in the best case. Also, the amount of uphill is limited with an additional problem: the safety system stops the robot if it detects something near it (in this case the ground).

So we decided to build a prototype of segway robot that could solve this problem by controlling its inclination independently. The chosen robot is inspired in a segway hoverboard, similar to the one appearing in Figure 2. The two wheels are controlled with classic control algorithms and the inclination of the central body is controlled with a flywheel mechanism that we will discuss in section 2.1.


Figure 2: Picture of a commercial segway hoverboard

Leaning Control


Figure 3: Isometric render view

# 2. Initial design considerations

The first thing we decided was the number of actuators. Most of segway robots include two motors for the motion control, but we added a third on in order to control the inclination. So we ended up with three motors in total because we want to control three degrees of freedom (inclination and speed of both wheels).

In order to control the inclination of the platform we needed to produce an external torque to the platform. We considered three methods: accelerating a flywheel, holding a pendulum in a non-vertical position and air friction with a fan. We discarded the last one due to the high speeds we needed to obtain a reasonable torque on the platform.
Both methods have strengths in different situations, so we decided to build a mixed piece that could combine both. The flywheel mode allows to deliver the maximum torque from the beginning but fails to deliver a continuous torque due to the motor achieving max speed. In the other hand the pendulum allows the system to apply a constant amount of torque over time.
We took two more restriction in our design. The first one symmetry along the motors/inclination axis in order to have an equilibrium in all possible inclinations without the need of external forces. We also took in consideration that some experiments may start produce arbitrary rotations of the platform, so none of the configurations should touch the ground to avoid crashes. Figure 6 illustrates this last restriction.
The design of the robot was done with the 3D design software Free-cad (https://www.freecadweb.org/) and most of the parts were 3D printed. 3D printing has also its own restrictions, for example not being able to print parts bigger than 25 cm. All part files are uploaded to the GitHub repository https://github.com/tarragoesteve/TFM under the hardware folder. So anyone can build this robot.
You can see the main views of an initial design on Figure 3, 4, 5 and 6.

## 2.1 Flywheel design

To control the inclination of the body two strategies are taken into account. Creating torque by a pendulum or accelerating the flywheel. In order to experiment with both of them we designed a part to allow both configurations by placing weights in different spots, see figure 7.

Figure 4: Front render view

Figure 5: Top render view.

Figure 6: Side render view.

Figure 7: Flywheel side render view.

Leaning Control

In order to create a configuration with maximum pendulum torque we have done the following com-putation. We denote the pendulum torque by τ , consider the masses are cylinders of mass mcylinder with radius rcylinder and width w and the radius of the flywheel is rflywheel. We want to place all N masses at the same distance of the center of the flywheel (rmax ) in a regular polygon except for one mass that will be at rmin. See figure 7.
Each mass weights:

mcylinder = ρ · w · π · r

2
cylinder
We neglect the mass of the flywheel structure versus the mass of the cylinders. All the gravitational torque is created by the cylinder masses and all of them are compensated with the opposite weight except for the two masses with different radius.
One of the weights can be placed along a track. The distance to the center will vary from rmin =

rcylinder + rmotor−axis ≈ rcylinder to rmax = rflywheel − rcylinder.

The maximum torque takes place when these two masses are aligned horizontal with respect to the ground and the movable weight is at distance rmin from the center.

τmax (rcylinder) = mcylinder · g · rmax − mcylinder · g · rmin = mcylinder · g · (rflywheel − 2 · rcylinder)

In order find the radius rc that maximizes τ we first compute the derivative:

∂τmax (rcylinder)
∂rc

= g · (

∂m
∂rc
- (rf − 2 · rc ) − mcylinder · 2)

∂mcylinder

∂rcylinder

= 2 · ρ · w · π · rcylinder

And make it zero to find the maximum:

∂τmax (rcylinder)

∂rcylinder

= 0

Substituting and simplifying we get:

∂m

∂rcylinder

·(rflywheel −2·rcylinder) = mcylinder ·2 ⇒ 2·ρ·w ·π ·rcylinder ·(rflywheel −2·rcylinder) = ρ·w ·π ·r

2
c

·2

⇒ rc · (rflywheel − 2 · rcylinder) = r

2
cylinder ⇒ (rflywheel − 2 · rcylinder) = rcylinder ⇒ rf = 3 · rcylinder

The circumradius R from the center of a regular polygon to one of the vertices is related to the side length s by:

R =

s
2 · sin π
n

R = rflywheel − rcylinder;; s = 2 · rcylinder

In our case:

Substituting in the circumradius equation we get n = 6, so we will use up to 6 masses in our flywheel.
We will have a variable number of masses N that we will be able to add to the flywheel as shown in the
following table:

Leaning Control

# 3. Optimization Setup

We want to size our design before building our prototype. We would like it to be optimal, so we have set up the requirements and the cost function we want to optimize.

## 3.1 Restrictions

The restrictions are a list of inequalities that our system has to fulfill. The first restriction is due to the initial design requirements. Finally, the other three are somehow arbitrary but will help us to reduce the size of the robot.

1. We will place our flywheel in a hole on our robot. We don’t want to touch the ground in any configuration so:

Figure 8: Flywheel hole diagram

rwheel >

r
(rflywheel + b)

2 + (h
2

)

2

2. Being able to insert the robot in to a wheel of diameter 0.5 m so:

Figure 9: External diameter diagram

0.25m >

q
r

2
wheel + L

2/4

3. We can place all electronic the devices:

L > 0.3m + w

4. Maximum weight of the robot: 5 kg

## 3.2 Requirements

We would like our robot to reach some mechanical specifications. These are related to mechanical equations that we will develop in the next section. They refer to the max speed, acceleration and terrain inclination the robot may achieve while controlling its platform inclination. We have divided our specifications in two blocks according to the two mechanisms.
Flywheel mode
1. yṁax (equation 10) > 0.1m/s.
2. y¨max (equation 9) > 1m/s

2
3. sin(αmax ) (equation 13) > 0.16.

Pendulum mode

1. yṁax (equation 12) > 1m/s.
2. y¨max (equation 11) > 0.1m/s

2
3. sin(αmax ) (equation 14) > 0.02.

## 3.3 Cost function

In addition to fulfilling the previous inequalities, we will adjust our design parameters [w (width of the cylinders), N(number of cylinders), r wheel and r flywheel] to minimize a cost function.
We will maximize the maximum sinus in the pendulum mode (equation 14) because it gives the robot the capacity to deliver force in a permanent state.
And we will also maximize the square of the max speed the robot can achieve in flywheel mode (equation
10) because it is proportional to the energy the robot can deliver using the flywheel at a certain moment.

Both equations try to maximize different modes so the robot we have a compromise between the two of them.

cost(rflywheel,rwheel,w, N) = −sin(αmax )pendulum − y˙

2
max−flywheel | (1)

In the next section we will find out what are the values of these equations with the construction parameters.

Leaning Control

# 4. Mechanical analysis

Once we know what we want to optimize, we need to know which is the relation with the design parameters. In this section we will analyze and understand the key dynamics of our robot, so we can choose the design parameters based on performance indicators. All the analysis is made supposing the inclination of the platform is maintained fixed. As parameters, we have the width of the flywheel masses w, the number of masses N, the radius of the flywheel rflywheel, and the radius of the wheels rwheel.

## 4.1 Inclination control

In order to keep the inclination of the platform at a certain angle φ we must be able to compensate all the torque being applied to the platform.

φ¨ · Iplatform = τplatform

Assuming that the platform is well-balanced (the center of masses is located at the rotation axis by our design restriction) and neglecting the torque generated by the friction with air, the sum of all the torques in the motor axis applied to the platform is equal to the sum of the torque applied by the motors:

τplatform =

Xτmotors

The torque that the motors deliver to the wheels and to the flywheel create a reaction in the platform in the opposite direction.

τplatform = −τmotor−right−wheel − τmotor−left−wheel − τmotor−flywheel

If we want keep the inclination φ, we must be able to cancel τplatform. Observe that the angular acceleration φ¨ of the platform is linearly dependent with the torque it receives.

0 = −τmotor−right−wheel − τmotor−left−wheel − τmotor−flywheel ⇒

τmotor−right−wheel + τmotor−left−wheel = −τmotor−flywheel

(2)

In other words, we must overpass the torque of the wheels with the torque of the flywheel if we want to control the inclination.

## 4.2 Wheels torque

The wheel torque we can induce is limited by the motor specifications. Note that the maximum torque of the motor is a function of velocity and in particular at max speed the torque is zero. See figure 10 to see the plot of this function.

τmotor−wheel(ωwheel)

We assume that the wheels just roll and do no slip. The robot is pushed by the wheels that make a force Ffriction against the ground in the contact point. See figure 11.

τmotor

ω

stall torque

maximum speed

Figure 10: Motor torque.

We can express the torque at the center of the wheel as:

τmotor−wheel + Ffriction · rwheel = Iwheel · ω˙ wheel

τmotor−wheel = Iwheel · w˙ wheel − Ffriction · rwheel | (3)

Figure 11: Wheel force diagram.

## 4.3 Flywheel torque

The flywheel torque we can induce is also limited by the motor specifications.
Assuming a general configuration of the flywheel where the moving mass is at distance r from the axis and angle θ, see figure 12, we formulate its torque the following way:

τmotor−flywheel + mcylinder · g · (r − rmax ) · sin θ = θ¨ · Iflywheel(r)

τmotor−flywheel = θ¨ · Iflywheel(r) + mcylinder · g · (rmax − r) · sin θ | (4)

Note that in equation 4 the two terms correspond to the two two mechanisms: acceleration of the flywheel and position of the pendulum.

Leaning Control

rmax; τmotor−flywheel

Figure 12: Flywheel diagram for N = 2

Figure 13: Wheel forward force diagram.

## 4.4 Maximum speed, acceleration and terrain inclination

In this subsection we would like to study the maximum speed and acceleration the robot may obtain in straight direction and the maximum terrain inclination it can stand on α.
We will assume both wheels turn at the same speed, have the same Ffriction and the same τwheel:

ωwheel−left = ωwheel−right = ωwheel

Applying Newton’s first law in the y-axis of figure 13:

y¨ · mtotal = 2 · Ffriction − mtotal · g · sin(α)

Substituting Ffriction taking in to account equation 3:

y¨ · mtotal = 2 ·

Iwheel · w˙ wheel − τmotor−wheel

rwheel

− mtotal · g · sin(α)

Using equation 2:

⇒ y¨ · mtotal =

2 · Iwheel · w˙ wheel

rwheel

+

τmotor−flywheel

rwheel

− mtotal · g · sin(α) | (5)

We will now study different cases to better understand this equation.

### 4.4.1 Speed and acceleration with no terrain inclination (α = 0)

The objective here is to obtain the maximum speed and acceleration we can get starting from rest in a plain surface.
The equation we get by substituting α = 0 in equation 5:

y¨ · mtotal =

τmotor−flywheel

rwheel

+

2 · Iwheel · w˙ wheel

rwheel

Substituting equation 4:

y¨ · mtotal =

θ¨ · Iflywheel(r) + mcylinder · g · (rmax − r) · sin θ

rwheel

+

2 · Iwheel · ω˙ wheel

rwheel

(6)

We will now split the study in two cases:

1. Flywheel case: r is fixed to r = rmax

Then:

y¨ · mtotal = −

¨θ · Iflywheel(rmax )

rwheel

+

2 · Iwheel · ω˙ wheel

rwheel

Taking in to account the following relation:

− ωwheel · rwheel = ẏ ⇒ −ω˙ wheel · rwheel = ÿ | (7)

Substituting in equation 6:

−ω˙ wheel · rwheel · mtotal =

¨θ · Iflywheel

rwheel

+

2 · Iwheel · ω˙ wheel

rwheel

−ω˙ wheel · (rwheel · mtotal +

2 · Iwheel

rwheel

) = θ¨ · Iflywheel

rwheel

We now define R as a non dimensional constant being the quotient between ẇwheel and −θ¨.

R =

ω˙ wheel
−θ¨

=

Iflywheel
r

2
wheel · mtotal + 2 · Iwheel

(8)

The moments of inertia are:

Iwheel ≈

1
2
- mwheel · r

2
wheel

Iflywheel ≈ N · mcylinder · r

2
max

Leaning Control

Substituting those in equation 8 we get:

R ≈

N · mcylinder · r

2
max
r

2
wheel · mtotal + 2 · Iwheel

< 1

We can see that R will always be smaller than 1 because N · mcylinder < mtotal and rmax < rwheel.

This means that the maximum acceleration of the wheels will be limited by the acceleration of the flywheel. The same is true for the speed.

In order to get the forward acceleration we can use equation 7

y¨ = −ω˙ wheel · rwheel = R ·

¨θ · rwheel

And using equation 4 we get that the maximum is:

τmotor(ω) = θ¨ · Iflywheel(r) ⇒ θ¨ =

τmotor(

˙θ)

Iflywheel(r)

y¨max = R ·

τmotor(

˙θ)

Iflywheel(r)

- rwheel

⇒ y¨max =

Iflywheel
r

2
wheel · mtotal + 2 · Iwheel

·

τmotor(

˙θ)

Iflywheel(r)

- rwheel

y¨max =

τmotor(

˙θ) · rwheel

r

2
wheel · mtotal + 2 · Iwheel

(9)

In order to compute the maximum speed we assume that the initial conditions are ˙θ = 0 and

ωwheel = 0

ωwheel−max =

Z t=tmax

t=0

ω˙ wheel · dt

Now we will proceed to do a change of variables in the integral.

∂ ˙θ
∂t

= θ¨ ⇒ dt =

d ˙θ
¨θ

ωwheel−max =

Z ˙θ= ˙θmax

˙θ=0

ω˙ wheel
θ¨
- d ˙θ =

Z ˙θ= ˙θmax

˙θ=0

−R · d ˙θ = −R ·

˙θmax

yṁax = rwheel · R ·

˙θmax | (10)

And ˙θmax is a limitation imposed by the motor specifications. Note that this is the maximum speed we can get using the flywheel system starting from rest.

2. Pendulum: ˙θ = 0, and r is fixed to r = rmin

Using equation 6 and θ¨ = 0

y¨ · mtotal =

mcylinder · g · (rmax − rmin) · sin θ

rwheel

+

2 · Iwheel · w˙ wheel

rwheel

Multiplying by rwheel both sides of the equation we get:

y¨ · mtotal · rwheel = mcylinder · g · (rmax − rmin) · sin θ + 2 · Iwheel · w˙ wheel

And using ẇwheel = −

y¨
rwheel

y¨ · mtotal · rwheel + 2 · Iwheel ·

y¨

rwheel

= mcylinder · g · (rmax − r) · sin θ

With some manipulation:

y¨ =

mcylinder · g · (rmax − rmin) · sin θ

mtotal · rwheel +

2·Iwheel
rwheel
Which is maximum when sin θ = 1

y¨max =

mcylinder · g · (rmax − rmin)·

mtotal · rwheel +

2·Iwheel
rwheel

(11)

Since the maximum acceleration obtained is constant, the speed could increase without limit. To get a meaningful estimation of the maximum speed, we will take into account the air friction that becomes more and more important as the speed increases.

Fdrag =

1
2
- ρ · CD · A · y˙

2

Adding this term to equation 5 we get:

y¨ · mtotal =

2 · Iwheel · w˙ wheel

rwheel

+

τmotor−flywheel

rwheel

− mtotal · g · sin(α) − Fdrag

And making ÿ = 0 and α = 0.

Fdrag =

τmotor−flywheel

rwheel

1
2
- ρ · CD · A · y˙

2 = mcylinder · g · (rmax − rmin) · sin(θ)/rwheel

The maximum ẏ is then obtained when θ =

π
2

:

yṁax =

s
2 · mcylinder · g · (rmax − rmin)

ρ · CD · A · rwheel

We will pick CD = 1, ρ = 1.2kg/m³

and A = 0.01m²
for our computations.
Also, note that the speed is also limited by maximum speed a motor can get ˙θmax .

yṁax = min(

˙θmax · rwheel,

s
2 · mcylinder · g · (rmax − rmin)

ρ · CD · A · rwheel

) | (12)

Leaning Control

### 4.4.2 Terrain inclination (α > 0)

The goal of this subsection is to study which is the maximum terrain inclination αmax on which the robot can stay, standing still without rolling down.
Substituting ÿ = 0 and ˙ωwheel = 0 in equation 5

0 =

τmotor−flywheel

rwheel

− mtotal · g · sin(α)

mtotal · g · sin(α) = τmotor−flywheel

rwheel

sin(α) = min(1, τmotor−flywheel

mtotal · g · rwheel

)

Substituting equation 4

sin(α) = min(1,

¨θ · Iflywheel(r) + mcylinder · g · (rmax − r) · sin θ

mtotal · g · rwheel

)

We are going to distinguish the same two cases as in the previous section:

1. Flywheel case: r is fixed to r = rmax The maximum inclination at a certain moment:

sin(αmax ) = min(1, θ¨ · Iflywheel

mtotal · g · rwheel

) = min(1, τmotor−flywheel(

˙θ)

mtotal · g · rwheel

) | (13)

This angle doesn’t give us a lot of information because it may not be fulfilled in a permanent state.

2. Pendulum: ˙θ = 0, and r is fixed to r = rmin

sin(α) = min(τmotor−flywheel, mcylinder · g · (rmax − rmin) · sin θ)

mtotal · g · rwheel

Which is maximum when sin θ = 1

sin(αmax ) = min(τmotor−flywheel, mcylinder · g · (rmax − rmin))

mtotal · g · rwheel

(14)

Note that the sin(αmax ) will not be more than 1.

# 5. Optimization Results

This section tries to find the optimal parameters given the equation that relate these parameters with the cost and the restriction defined before.
Our procedure has been making a grid with the four parameters of the robot design: w (width of the cylinders), N(number of cylinders), rwheel and rflywheel. We have fixed rflywheel to a number of discrete values between 0.05 and 0.125 and, for each one, we evaluate the cost for each point of the grid, remove those which do not fulfill the restrictions, and keep the configuration providing the minimum cost.

Figure 14: Plot of the wheel radius and the width of the cylinder that was optimal for each flywheel radius.

We can observe that the relation between the flywheel radius and the wheel radius is linear. This is because we are always on the edge of the restriction number one.

Leaning Control


Figure 15: Plot of the N that minimize the cost function.

Figure 16: Plot of the equations 10 and 12 at the parameters that minimize the cost function and fullfil the requirements and restrictions

In this figure we can observe that the speed of in the pendulum mode increases linearly with the flywheel radius. This is because it is linearly related with the wheel radius.


Figure 17: Plot of the equations 9 and 11 at the parameters that minimize the cost and fulfill the requirements and restrictions


Figure 18: Plot of the equations 13 and 14 at the parameters that minimize the cost and fulfill the requirements and restrictions

We can see in figure 18 that when the flywheel radius exceeds 0.07 m the requirement of the flywheel sinus becomes active.

Leaning Control

Figure 19: Plot of the mass for each configuration.

We can see in figure 19 that the total mass never exceeds the 5 kg limit.


Figure 20: Plot of the equation 1 for each configuration.

Seeing the parameters that minimize cost and the material that we had available our selected parameters were:

rflywheel | rwheel | w | N
8cm | 10cm | 5cm | 2

With these parameters we get the following specifications:

Total mass | 2,91 kg
Pendulum
Maximum sinus | 0,042
Maximum speed horizontal | 1,84 m/s
Maximum acceleration horizontal | 2 0,38 m/s
Flywheel
Maximum sinus | 0,171
Maximum speed horizontal | 0,24 m/s
Maximum acceleration horizontal | 1.52 m/s 2

Leaning Control

# 6. Rectilinear movement dynamics with rflywheel fixed

This section studies the dynamics of the robot and the transition between states to answer questions as how fast can we reach the maximum speed or how quickly can we accelerate during a concrete period. In order to study the dynamics of the robot we will use Lagrange mechanics. To reduce the number of variables we will study the case of rectilinear movement by imposing that both wheels turn at the same speed. We will also set the radius of the free weight to rflywheel. Note that in this analysis the platform is not assumed to keep a fixed inclination as before, but it is allowed to rotate.
The generalized coordinates (q) will be:
1. φground−wheel: rotation of the wheel respect the ground.
2. φwheel−platform: rotation of the platform respect the wheel.
3. φplatform−flywheel: rotation of the flywheel respect the platform.

We will use two auxiliary variables:

1. φground−platform = φground−wheel + φwheel−platform: rotation of the platform respect the ground.
2. φground−flywheel = φground−platform + φplatform−flywheel: rotation of the flywheel respect the ground.

The total potential energy:

V = mcylinder · (rflywheel − rflywheel−max ) · cos(φground−flywheel) · g | (15)

The total kinetic energy:

T =

1
2

·[φ˙²

ground−wheel ·Iwheel+φ˙²

ground−platform·Iplatform+φ˙²

ground−flywheel ·Iflywheel+φ˙² ground−wheel ·r

2
| wheel ·mtotal]
(16)
The Lagrangian is defined as:
L = T − V | (17)

Lagrange’s equation is:
d
dt(

∂L
∂q˙j

) = ∂L
∂qj
+ Fj | (18)

So in our case:

∂L
∂φ˙
ground−wheel

= φ˙

ground−wheel·Iwheel+φ˙

ground−platform·Iplatform+φ˙

ground−flywheel·Iflywheel+φ˙ | ground−wheel·r
| 2
| wheel·mtotal

(19)
∂L
∂φ˙
wheel−platform

= φ˙

ground−platform · Iplatform + φ˙
ground−flywheel · Iflywheel | (20)

∂L
∂φ˙
platform−flywheel

= φ˙
ground−flywheel · Iflywheel | (21)

We define M as the following matrix:

Iwheel + Iplatform + Iflywheel + r

2
wheel · mtotal | Iplatform + Iflywheel | Iflywheel
Iplatform + Iflywheel | Iplatform + Iflywheel | Iflywheel
Iflywheel | Iflywheel | Iflywheel
- (22)

In matrix form and with our generalized coordinates:

∂L
∂q˙
= M · q˙ | (23)

d
dt(

∂L
∂q˙
) = M · q¨ | (24)

Let a be a constant:

a = mcylinder · (rflywheel − rflywheel−max ) · g | (25)

∂L
∂q

= a · sin(φground−flywheel) ·

1
1
1
- (26)

So using Lagrange’s equation we get:

M · q¨ = a · sin(φground−flywheel) ·

1
1
1
- + F | (27)

## 6.1 Simulations

In this subsection we study different policies for the generalized forces (F) applied to the robot in rectilinear movement case.
The robot has 2 actuators, the motors between the wheel and the platform and the motor between the flywheel and the platform. All motors in the systems have a limited torque related with the speed as you may see in Figure 10.

F =

0

τwheel−platform

τplatform−flywheel

- (28)

In order to compare the different policies we compare their efficiency in performing the same task: The robot must travel 30 radians (3 meters) and stop at the end. All the parameters from the simulation are set equal to the values found in section 5. Keep in mind that the wheel radius is 10 cm.
Here you can see a table that summarize the results:

Leaning Control

Experiment | Total time(s) | Time to max speed(s) | Max speed(rad/s) | Time to brake(s)
Controlling inclination
Flywheel | 12,45 | 0,7 | 2,45 | 0,15
Pendulum | 5,59 | 2,69 | 10,36 | 2,90
Waitress | 8,24 | 4,12 | 5,49 | 4,12
Free inclination
Double flywheel | 3,9 | 1 | 8,51 | 0.27
Compose mechanism | 3,82 | 2,3 | 10,2 | 2,04

### 6.1.1 Controlling the platform inclination

In the first two experiments we want to keep the platform in a horizontal position. That’s the reason why we force the τwheel−platform equal to τplatform−flywheel in the experiments flywheel and pendulum.

1. Flywheel

The movable weight is fixed at rmax . In this experiment we consign the platform-flywheel motor to output the maximum possible torque. Then the platform-wheels motors deliver the same torque. The platform-flywheel motor reaches in less than one second the maximum speed. This then limits the wheel-platform speed because no more torque can be applied one that point is reached.


Figure 21: Plot of the angles for the flywheel experiment.

Figure 22: Plot of the angular velocities for the flywheel experiment.

2. Pendulum

The movable weight is fixed at rmin. In this experiment we consign the platform-flywheel motor to get to 90 with a PID controller. Then the platform-wheels motors deliver the same torque. The robot does not accelerate as fast as in the flywheel experiment but reaches a higher speed that allows it to travel the distance in less time. Note that the robot could have kept accelerating but had to brake before reaching the maximum speed.


Figure 23: Plot of the angles for the pendulum experiment.

Leaning Control


Figure 24: Plot of the angular velocities for the pendulum experiment.

3. Waitress

The movable weight is fixed at rmin. This experiment is different from the previous two and its aim is to illustrate how the robot could follow and inclination consign. The experiment is designed the following way. A set point torque is given to the wheel-platform and the flywheel-motor PID has an inclination consign too. The inclination consign is such that the sum of accelerations received from and object in the platform is perpendicular to the platform.

Figure 25: Plot of the angles for the waitress experiment.


Figure 26: Plot of the angular velocities for the waitress experiment.

### 6.1.2 Letting the platform turn

In this experiment we take advantage of the fact that the platform may not be needed to stay horizontal in some displacement. The robot uses the platform as an additional flywheel to help the robot accelerate and brake.

1. Double Flywheel

The movable weight is fixed at rmax . In this experiment we add the flywheel turn over the platform turn to create more torque to accelerate our wheels. We always do the maximum possible torque with all the motors.

Leaning Control

Figure 27: Plot of the angles for the double flywheel experiment.


Figure 28: Plot of the angular velocities for the double flywheel experiment.

2. Compose

The movable weight is fixed at rmin. In this experiment we add the pendulum effect to the flywheel effect produced by the flywheel. We do so with a PID controller for the angle ground-flywheel and making the maximum possible torque with the platform-wheel motors.


Figure 29: Plot of the angles for the compose experiment.

Figure 30: Plot of the angular velocities for the pendulum experiment.

Leaning Control

# 7. Flywheel brake study

The problem with the flywheel method is that, when it reaches the maximum speed, the motor cannot apply torque. This section aims to study a possible way to break the flywheel without applying torque to the platform. The idea is combining both methods: we will leave the moving weight free.
The initial hypothesis was: If we let weight move, when it is going upward will have a larger radius than when is going downward and will produce an average external torque against the movement of the flywheel. From an energetic point of view we are transforming the rotation energy of the flywheel in to translation of the free cylinder and then releasing it trough collisions.

## 7.1 System of differential equations

To simplify the experiment we will assume that the platform inclination is constant and that the motor is not producing any torque to the platform.
As described in figure 12 we will use two variables to describe the flywheel position: r and θ.
Using equation 4:

τmotor−flywheel = θ¨ ∗ Iflywheel(r) + mcylinder ∗ g ∗ (rmax − r) ∗ sin(θ)

θ

r

m ∗ g

m ∗ r ∗ ˙θ
2

z

y

Figure 31: Cylinder force diagram.

As seen in figure 31, we can deduce Newton’s equation for the distance from the cylinder to the center
r. Note that we are adding the centrifugal force term due to the non-inertial frame.

¨r ∗ m = −m ∗ g ∗ cos(θ) + m ∗ r ∗ ˙θ
2

¨r = −g ∗ cos(θ) + r ∗ ˙θ
2

The variables we will be using for our ODE system are: r,ṙ,θ,

˙θ.

Note that we impose τflywheel = 0 so the motor is not applying any torque.

r˙ = ṙ
¨r = −g ∗ cos(θ) + r ∗ ˙θ
2
˙θ = ˙θ

θ¨ =

mcylinder ∗g∗(r−rmax )∗sin θ

Iflywheel (r )

Our initial conditions will be the free cylinder mass lying on the bottom of the flywheel and the flywheel turning at a speed θ0:

r = rmax
r˙ = 0
θ = π
˙θ = θ0

We will use a Poincaré map to simulate the bounce with the end of the guides at r = rmin and r = rmax . At each bounce we will reduce its kinetic energy by a percentage bounce percentage.

## 7.2 Results

The parameters of the simulation where:

rflywheel = 8cm
rwheel = 9cm
w = 7cm
˙θ0 = 4.2πrad/s

bounce percentage = 0.0(totally inelastic)


Figure 32: How the variable ˙θ evolve over time

As we can see in figure 32 the flywheel is braking until it becomes a pendulum and starts oscillating.

Leaning Control


Figure 33: How the variable r evolves over time

In the first laps the cylinder is almost always at the maximum value of r, but as the speed decreases each lap the value of r decreases until it hits the rmin. In other words, at the beginning is operating as a flywheel but then thanks to the collisions it becomes a pendulum.

Figure 34: How the variable r evolve over θ zoomed

In image 34 we can appreciate that the r decreases slower than what it increases.


Figure 35: How the variable θ evolves over time.


Figure 36: How the variable r evolves over θ.

Leaning Control

# 8. Rectilinear movement with rflywheel free

In this section we have developed the Lagrange Mechanics for the system with one mass of the flywheel being free (i.e. Movable along a rail).
The generalized coordinates (q) will be:
1. φground−wheel: rotation of the wheel respect the ground.
2. φwheel−platform: rotation of the platform respect the wheel.
3. φplatform−flywheel: rotation of the flywheel respect the platform.
4. r: distance from the center of the flywheel to the free cylinder.

We will use two auxiliary variables:

1. φground−platform = φground−wheel + φwheel−platform: rotation of the platform respect the ground.
2. φground−flywheel = φground−platform + φplatform−flywheel: rotation of the flywheel respect the ground.

The total potential energy:

V = mcylinder · (r − rflywheel−max ) · cos(φground−flywheel) · g | (29)

The total kinetic energy:

T =

1
2
- [φ˙²

ground−wheel · Iwheel + φ˙²

ground−platform · Iplatform + φ˙² ground−flywheel · Iflywheel(r)

+ φ˙²
ground−wheel · r

2
wheel · mtotal + ṙ

2
- mcylinder] (30)

The Lagrangian is defined as:
L = T − V | (31)

Lagrange’s equation is:
d
dt(

∂L
∂q˙j

) = ∂L
∂qj
+ Fj | (32)

So in our case:

∂L
∂φ˙
ground−wheel

= φ˙

ground−wheel · Iwheel + φ˙ ground−platform · Iplatform

+ φ˙

ground−flywheel · Iflywheel(r) + φ˙ ground−wheel · r

2
wheel · mtotal (33)

∂L
∂φ˙
wheel−platform

= φ˙

ground−platform · Iplatform + φ˙
ground−flywheel · Iflywheel(r) | (34)

∂L
∂φ˙
platform−flywheel

= φ˙
ground−flywheel · Iflywheel(r) | (35)

∂L
∂r˙
= ṙ · mcylinder | (36)

We define M as the following matrix:

Iwheel + Iplatform + Iflywheel(r) + r

2
wheel · mtotal | Iplatform + Iflywheel(r) Iflywheel(r) | 0
Iplatform + Iflywheel(r) | Iplatform + Iflywheel(r) Iflywheel(r) | 0
Iflywheel(r) | Iflywheel(r) | Iflywheel(r) | 0
0 | 0 | 0 | mcylinder

(37)

In matrix form and with our generalized coordinates:

∂L
∂q˙
= M · q˙ | (38)

d
dt(

∂L
∂q˙

) = M · q¨ + M˙
- q˙ | (39)

Let’s recall the definition of Iflywheel(r)

Iflywheel(r) = mcylinder · r

2 + C | (40)

Compute the derivative
˙
Iflywheel(r) = 2 · mcylinder · r · r˙ | (41)

We compute M˙ as the following matrix:

M˙ = ˙
Iflywheel(r) ·

1 1 1 0
1 1 1 0
1 1 1 0
0 0 0 0

(42)

Let a be::
∂L

∂q1..3

= a = mcylinder · (r − rflywheel−max ) · g · sin(φground−flywheel) | (43)

Let b be:
∂L
∂r

= b = ·mcylinder · r · φ˙²
ground−flywheel − mcylinder · g · cos(φground−flywheel) | (44)

∂L
∂q

=

a
a
a
b

(45)

So using Lagrange’s equation we get:

M · q¨ + M˙
- q˙ =

a
a
a
b

+ F | (46)

Leaning Control

# 9. Components

In this section we will explain all the components used during the building of the robot, how we build them and which is its function.

## 9.1 Mechanical components

These components do not have any electronics and the important thing about them is their mechanical function.

### 9.1.1 Central Body

Used to host the flywheel, a motor and a bearing. It also has lateral tabs so it can easily be joined with the lateral body part. It’s 3D printed and in the same orientation you see in figure 37.

Figure 37: 3D Model of the central body.

### 9.1.2 Lateral Body

Used to host the wheel motor and the rest of the electronic components. It also has lateral tabs so it can easily be joined with the central body part. It’s 3D printed and in the same orientation you see in figure 38.


Figure 38: 3D Model of lateral body.

### 9.1.3 Wheels

The wheels are 3D printed. The orientation we used to print them is putting the motor axis vertical. Each wheel is produced by two symmetric parts that are glued together around the motor.


Figure 39: 3D Model of a wheel.

### 9.1.4 Flywheel

The flywheel is composed by 3 parts:

1. 3D printed wheels very similar to the one in figure 39
2. Steel bolts, washers and nuts.
3. Metallic axis.

Leaning Control

### 9.1.5 Bearings

We are using angular balls bearing as the one seen in the figure 40 to surround the flywheel axis. This bearing is tight fit in to the 3D printed central body. The main purpose of the bearing is to support the flywheel metal axis and help the motor with the flywheel weight stress.

Figure 40: Photo of a bearing.

### 9.1.6 Reinforcements

After we built the first prototype, we saw that the robot was suffering from bending. So we decided to reinforce the structure with additional 3D printed tabs and two aluminum ’U’ profiles to solve the problem.

## 9.2 Electronic components

### 9.2.1 Raspberry Pi

The Raspberry Pi is a small single-board computer. We are using Raspberry Pi 3 Model B. It has some features that we will use:

- GPIO pins: General Purpose Input/ Output pins are used to communicate with the motors and other peripherals.
- Ethernet connection: We used to be able to set up the Wi-Fi’s connection.
- Wi-Fi’s connection: We used to be able to control the robot without cables.
- 5V and 3V lines: It’s useful to get the 3V to power the encoders.
- DC’s hardware power: So we can power the Raspberry the same way as the other electronic components.
- I2C: I2C is a serial protocol for two-wire interface to connect low-speed devices like micro-controllers. We use it to communicate the Raspberry Pi


Figure 41: Raspberry Pi picture

Weight | 42 g
Price per unit | 35 euros
Number of units | 1

### 9.2.2 Batteries

We are using four identical batteries to power our system. They are commercial external power supplies for smartphones. They can be recharged via a micro-USB. We use USB cables to transmit the power to an outlet that connects two batteries in series that power the DC Bridges. These bridges are powering the motors and the Raspberry.
These batteries do not always work as expected because they have integrated security measures that disconnect them when they detect that not power is being used.
In the other hand they incorporate many features as battery level indicator, incorporated recharge mechanisms and on/off buttons.
Weight | 200 g
Price per unit | 10 euros
Number of units | 4

### 9.2.3 Printed Circuit Board

In this project we tested the basic electronic with a breadboard, once we knew the electronic components where working we decided to transfer our circuit to a Printed Circuit Board (PCB). In particular, we used a Double Sided PCB that allows routing traces in both sides.

Leaning Control

Figure 42: Printed circuit board
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

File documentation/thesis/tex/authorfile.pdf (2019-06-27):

## Universitat Polit`ecnica de Catalunya

## Facultat de Matem`atiques i Estad´ıstica

## Master in Advanced Mathematics and Mathematical Engineering

# Master’s thesis

# A Remotely-driven Hoverboard With Platform Leaning Control

## Esteve Tarrag´o

## Supervised by Advisor: Enric Celaya, Tutor: Merc`e Oll`e

## June, 2019

Thanks to Patrick Grosch, Llu´ıs Ros, Enric Celaya, I˜nigo Moreno
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

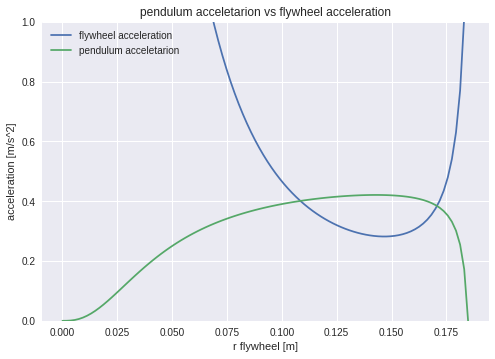
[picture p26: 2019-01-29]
documentation/thesis/tex/img/pendulum_accel_r_flywheel.png

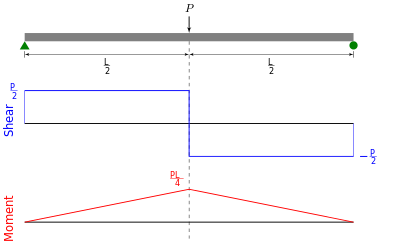
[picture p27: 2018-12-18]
documentation/thesis/tex/img/Shear_Moment_Diagram.png

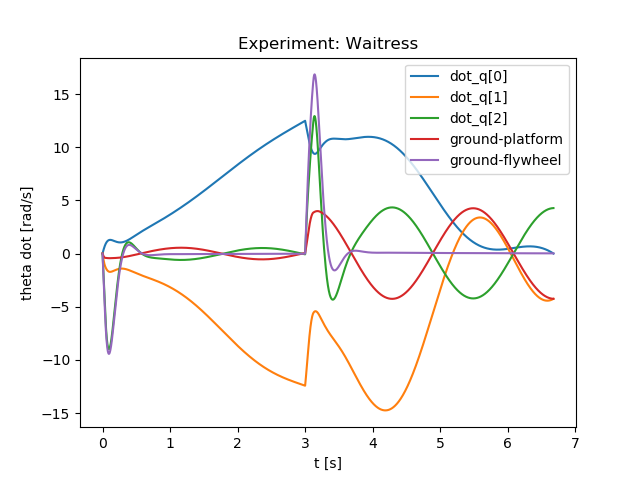
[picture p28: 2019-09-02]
documentation/thesis/tex/img/3_modes/waitress_qdot.png

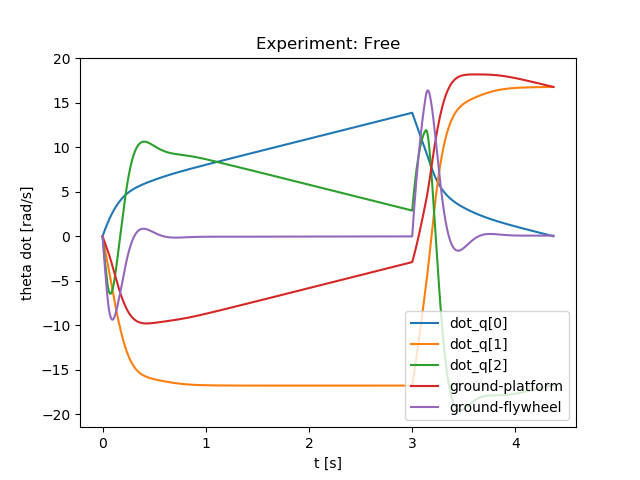
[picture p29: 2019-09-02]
documentation/thesis/tex/img/3_modes/free_qdot.png

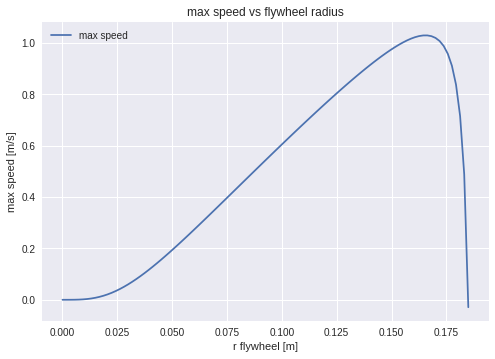
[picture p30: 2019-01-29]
documentation/thesis/tex/img/max_speed_r_flywheel.png

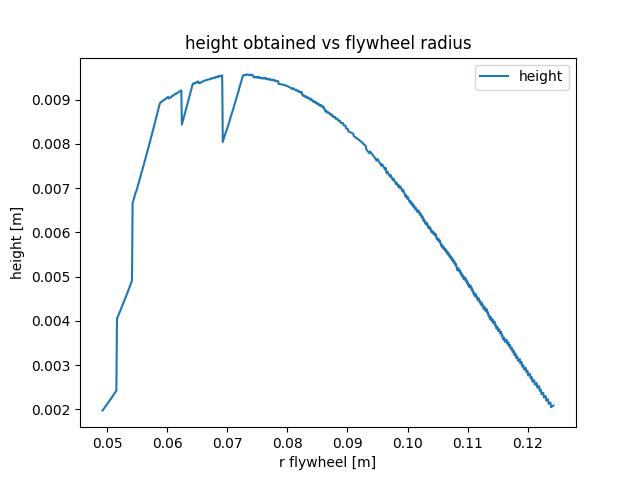
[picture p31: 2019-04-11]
documentation/thesis/tex/img/optimization/height.png

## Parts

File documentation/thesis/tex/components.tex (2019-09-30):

\section{Components}
In this section we will explain all the components
used during the building of the robot, how we build them and which is
its function.

\subsection{Mechanical components}
These components do not have any electronics and the important
thing about them is their mechanical function.
\subsubsection{Central Body}

Used to host the flywheel, a motor and a bearing. It also has lateral
tabs so it can easily be joined with the lateral body part.
It's 3D printed and in the same orientation you see in figure
\ref{fig: central body}.
\begin{figure}[H]
    \centering
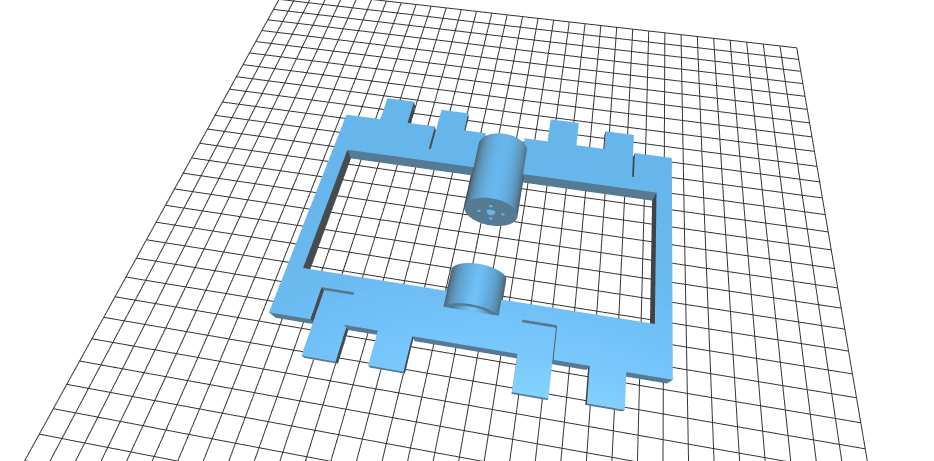
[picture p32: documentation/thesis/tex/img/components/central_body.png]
    
    \caption{3D Model of the central body.}
    \label{fig: central body}
\end{figure}

\subsubsection{Lateral Body}
Used to host the wheel motor and the rest of the electronic components.
It also has lateral tabs so it can easily be joined with the central body part.
It's 3D printed and in the same orientation you see in figure
\ref{fig: lateral body}.
\begin{figure}[H]
    \centering
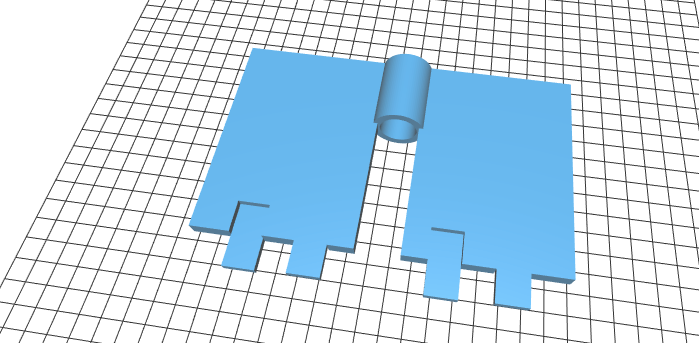
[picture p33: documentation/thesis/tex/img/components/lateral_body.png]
    
    \caption{3D Model of lateral body.}
    \label{fig: lateral body}
\end{figure}
\subsubsection{Wheels}
The wheels are 3D printed. The orientation we used to print them
is putting the motor axis vertical. Each wheel is produced by two
symmetric parts that are glued together around the motor.
\begin{figure}[H]
    \centering
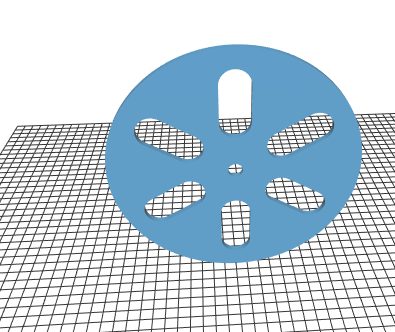
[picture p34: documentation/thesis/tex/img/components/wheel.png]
    
    \caption{3D Model of a wheel.}
    \label{fig: 3D wheel}
\end{figure}
\subsubsection{Flywheel}
The flywheel is composed by 3 parts:
\begin{enumerate}
    \item 3D printed wheels very similar to the one in figure \ref{fig: 3D wheel}
    \item Steel bolts, washers and nuts.
    \item Metallic axis.
\end{enumerate}
\subsubsection{Bearings}
We are using angular balls bearing as the one seen in the figure
\ref{fig: photo bearing} to surround the flywheel axis. This bearing is
tight fit in to the 3D printed central body. The main purpose of the bearing
is to support the flywheel metal axis and help the motor with the flywheel weight
stress.
\begin{figure}[H]
    \centering
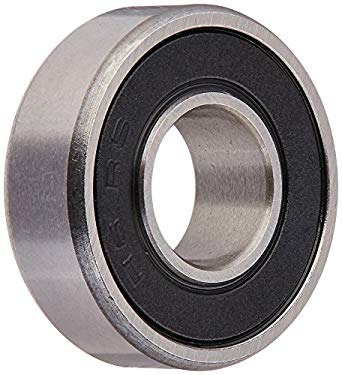
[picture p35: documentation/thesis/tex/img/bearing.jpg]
    
    \caption{Photo of a bearing.}
    \label{fig: photo bearing}
\end{figure}
\subsubsection{Reinforcements}
After we built the first prototype, we saw that the robot was suffering
from bending. So we decided to reinforce the structure with additional 3D
printed tabs and two aluminum 'U' profiles to solve the problem.

\subsection{Electronic components}
\subsubsection{Raspberry Pi}
The Raspberry Pi is a small single-board computer.
We are using Raspberry Pi 3 Model B. It has some features that we will use:
\begin{itemize}
    \item GPIO pins: General Purpose Input/ Output pins are used to
    communicate with the motors and other peripherals.
    \item Ethernet connection: We used to be able to set up the Wi-Fi's connection.
    \item Wi-Fi's connection: We used to be able to control the robot without cables.
    \item 5V and 3V lines: It's useful to get the 3V to power the encoders.
    \item DC's hardware power: So we can power the Raspberry the same way as the
          other electronic components.
    \item I2C: I2C is a serial protocol for two-wire interface to
          connect low-speed devices like micro-controllers. We use it to communicate
          the Raspberry Pi
\end{itemize}
\begin{figure}[H]
    \centering
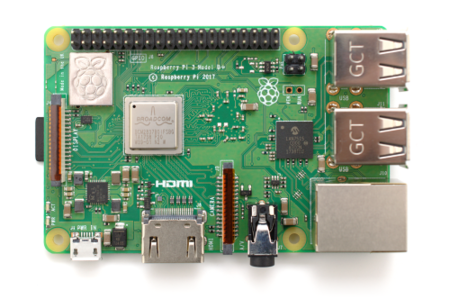
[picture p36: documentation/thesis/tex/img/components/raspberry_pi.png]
    
    \caption{Raspberry Pi picture}
    \label{fig:}
\end{figure}
\begin{center}
    \begin{tabular}{ |c|c| }
        \hline
        Weight          & 42 g     \\
        \hline
        Price per unit  & 35 euros \\
        \hline
        Number of units & 1        \\
        \hline
    \end{tabular}
\end{center}
\subsubsection{Batteries}
We are using four identical batteries to power our system. They are
commercial external power supplies for smartphones. They can be recharged
via a micro-USB. We use USB cables to transmit the power to an outlet
that connects two batteries in series that power the DC Bridges.
These bridges are powering the motors and the Raspberry.

These batteries do not always work as expected because they have
integrated security measures that disconnect them when they detect
that not power is being used.

In the other hand they incorporate many features as battery level
indicator, incorporated recharge mechanisms and on/off buttons.
\begin{center}
    \begin{tabular}{ |c|c| }
        \hline
        Weight          & 200 g    \\
        \hline
        Price per unit  & 10 euros \\
        \hline
        Number of units & 4        \\
        \hline
    \end{tabular}
\end{center}
\subsubsection{Printed Circuit Board}
In this project we tested the basic electronic with a breadboard, once we knew
the electronic components where working we decided to transfer our circuit to
a Printed Circuit Board (PCB). In particular, we used a Double Sided PCB that
allows routing traces in both sides.
\begin{figure}[H]
    \centering
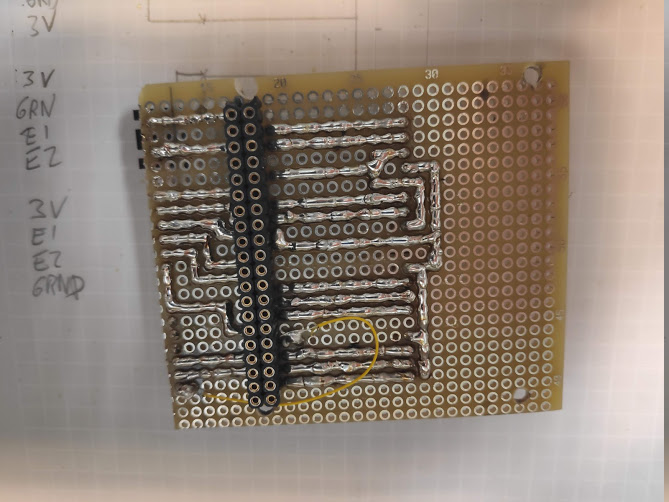
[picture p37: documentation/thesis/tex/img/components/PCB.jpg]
    
    \caption{Printed circuit board}
    \label{fig: PCB}
\end{figure}

\subsubsection{DC Motor}
A DC Motor is a rotary electric machine that transforms electrical energy
(in the form of direct current) into mechanical energy through electromagnetic interactions.

Here are the specifications of our three motors:

\begin{center}
    \begin{tabular}{ |c|c| }
        \hline
        Operating voltage       & between 3 V and 9 V \\
        \hline
        Free-run speed at 6 V   & 176 RPM             \\
        \hline
        Free-run current at 6 V & 80 mA               \\
        \hline
        Stall current at 6V     & 900 mA              \\
        \hline
        Stall torque at 6V     & 5 kg·cm             \\
        \hline
        Gear ratio              & 1:35                \\
        \hline
        Reductor size           & 21 mm               \\
        \hline
        Weight                  & 85 g                \\
        \hline
        Price per unit          & 10 euros            \\
        \hline
        Number of units         & 3                   \\
        \hline
    \end{tabular}
\end{center}

\begin{figure}[H]
    \centering
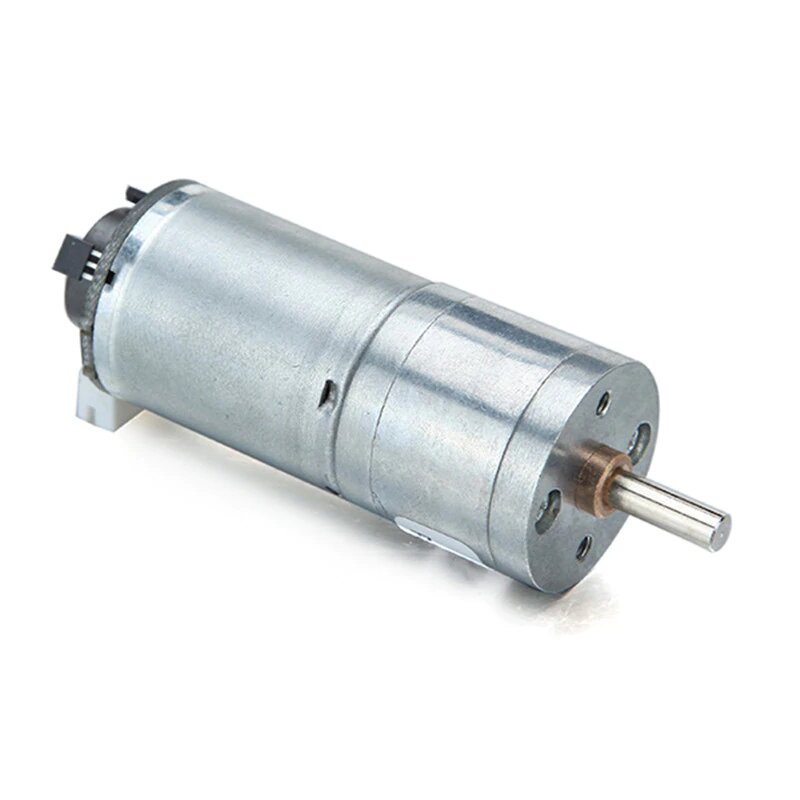
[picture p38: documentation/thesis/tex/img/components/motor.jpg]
    
    \caption{DC Motor}
    \label{fig: DC Motor}
\end{figure}

\subsubsection{H Bridge}
An H bridge is an electronic circuit that switches the polarity of a
voltage applied to a load (in our case DC motors). This allows the motor to
go forwards and reverse.

Also, it has the possibility to modulate the output power through a PWM signal.

Our particular H Bridge (L298N) is capable of supporting two motors at the same time.
This means that it has 6 input signals, 2 PWM (one for each motor) and 4 enable signals
(2 for each motor).

The input power for the H bridge is 10V but it has losses and it delivers around 8,5 V to the motors.
Also, it has a 5V power output that we used to feed the Raspberry Pi.

\begin{figure}[H]
    \centering
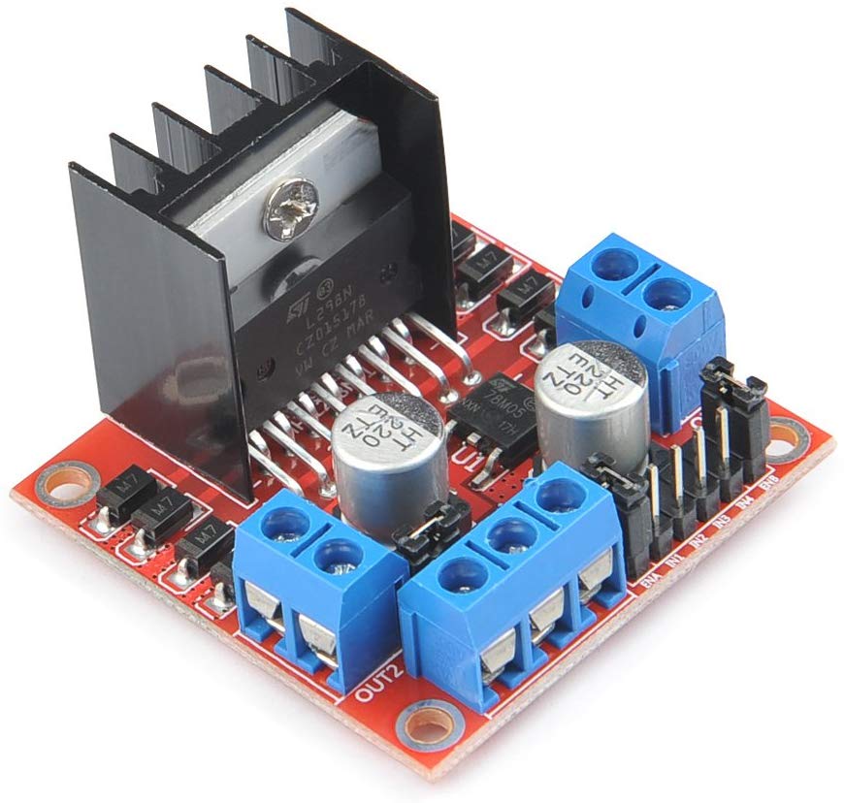
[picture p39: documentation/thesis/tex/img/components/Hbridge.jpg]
    
    \caption{H Bridge}
    \label{fig: H Bridge}
\end{figure}

\subsubsection{Rotatory Encoder}
A rotary encoder, also called a shaft encoder, is an electro-mechanical device that converts the
angular position or motion of a shaft or axle to analog or digital output signals.

Our encoder has two signals, channel A and channel B offset by 90
degrees (in quadrature). The direction of rotation can be determined
by which channel is leading. If channel A is leading, the
direction is taken to be clockwise, and if channel B is
leading, the direction is counterclockwise. 

\begin{figure}[H]
    \centering
    
    \caption{Encoder Signals. Image credit: National Instruments Corporation.}
    \label{fig: Encoder}
\end{figure}

We programmed an interruption that fires every time a channel changes the state.
It increments (or decrements) a counter, so we can then compute the position and
the speed of each motor.

\subsubsection{Accelerometer}
An accelerometer is a device that measures proper acceleration. The one we are using is MPU-6050.
We use the acceleration measured by the accelerometer to know in which inclination
is the platform. The accelerometer is connected to the Raspberry Pi via I2C.

\begin{figure}[H]
    \centering
    
    \caption{Pictures of a MPU-6050}
    \label{fig: MPU-6050}
\end{figure}

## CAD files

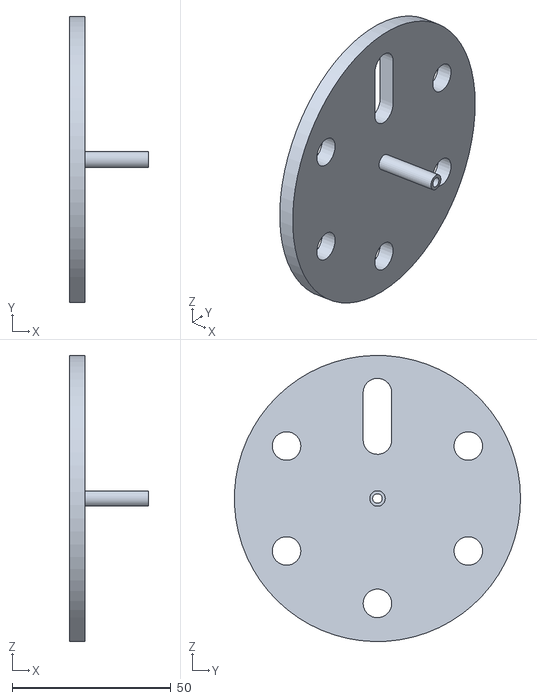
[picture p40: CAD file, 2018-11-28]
hardware/right_fly_wheel.stl
25.0 x 90.0 x 90.0

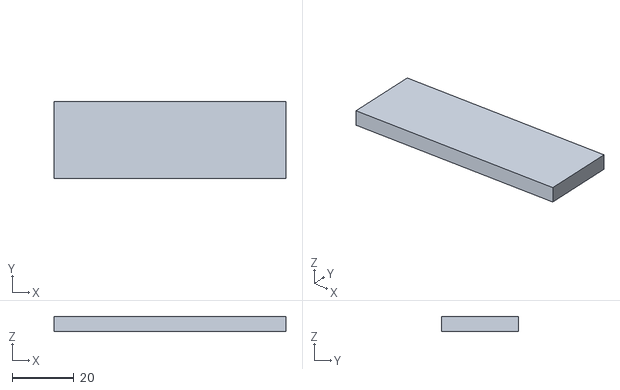
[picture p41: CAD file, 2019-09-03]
hardware/v2/reinforcement.stl
75.0 x 25.0 x 5.00

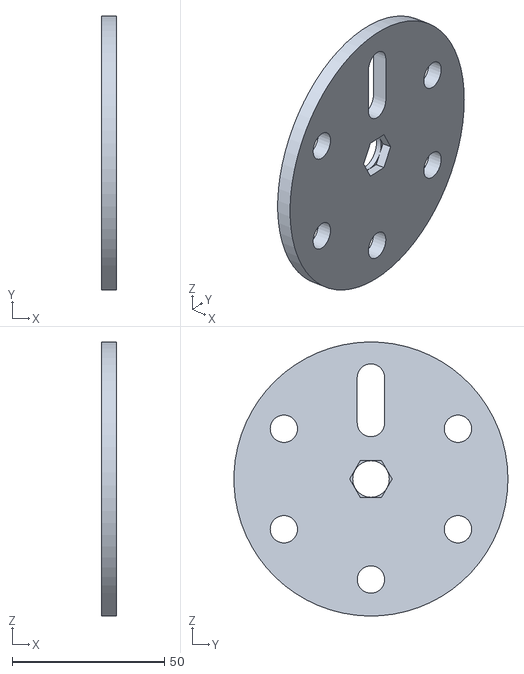
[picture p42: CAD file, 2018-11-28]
hardware/left_fly_wheel.stl
5.00 x 90.0 x 90.0

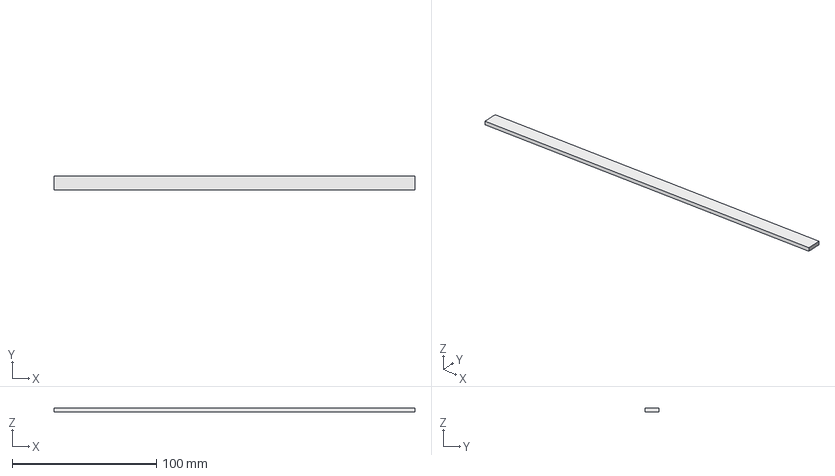
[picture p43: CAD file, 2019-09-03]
hardware/v2/U support.FCStd
250.0 x 10.0 x 2.50 mm

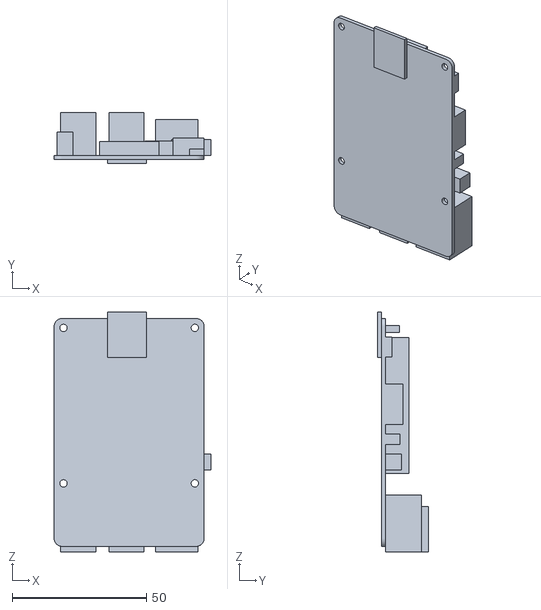
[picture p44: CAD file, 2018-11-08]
hardware/Rough Pi Model.stl
58.5 x 18.9 x 89.5

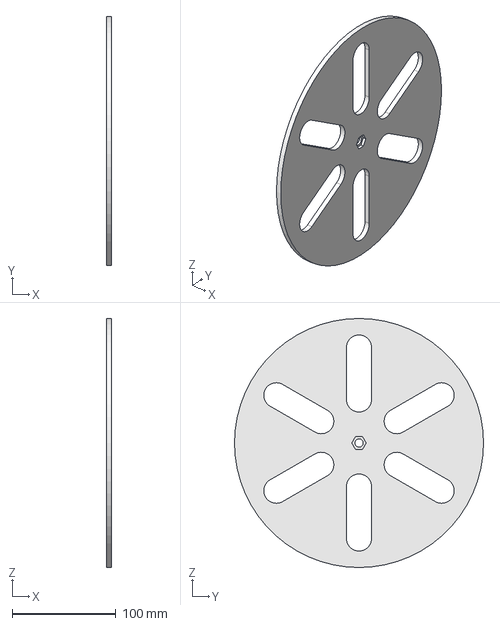
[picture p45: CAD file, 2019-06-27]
hardware/v2/robot.fcstd
5.00 x 240.0 x 240.0 mm

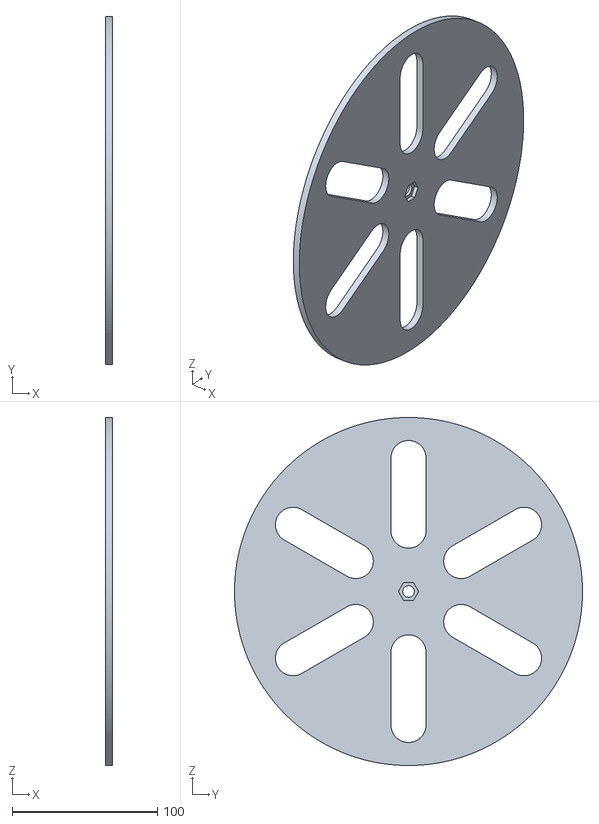
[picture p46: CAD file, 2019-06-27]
hardware/v2/big_wheel_exterior.stl
5.00 x 240.0 x 240.0

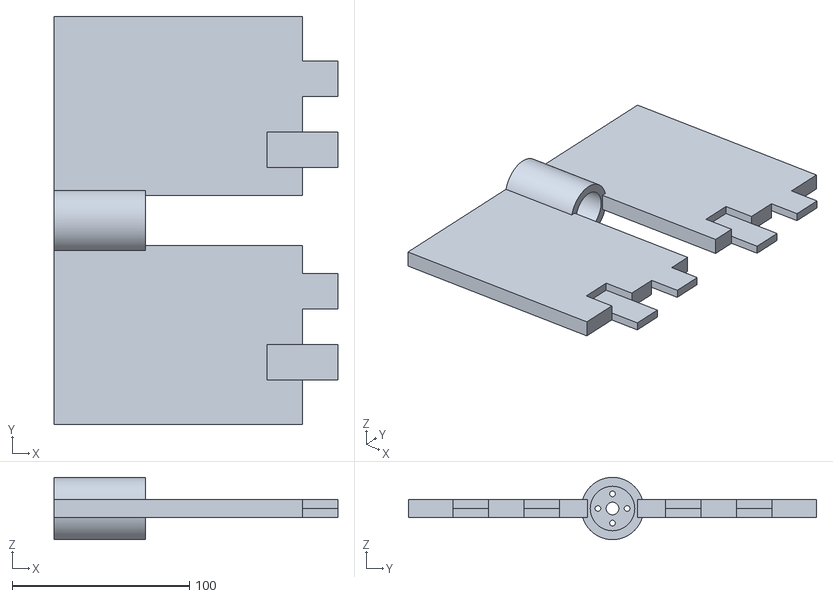
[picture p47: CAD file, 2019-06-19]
hardware/v2/lateral_body.stl
160.0 x 230.0 x 35.1

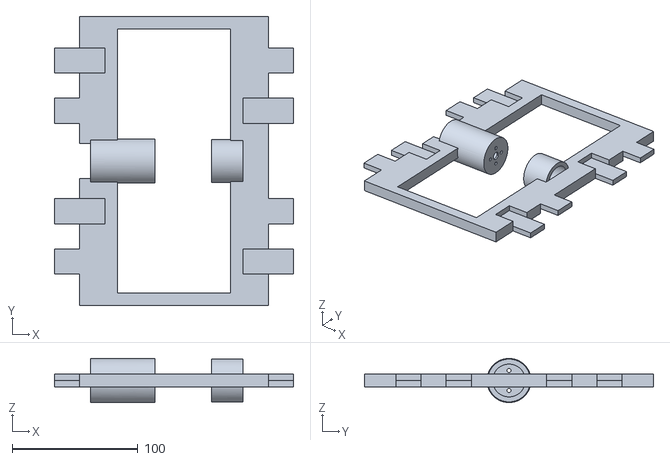
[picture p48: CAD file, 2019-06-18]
hardware/v2/central_body.stl
190.0 x 230.0 x 35.1

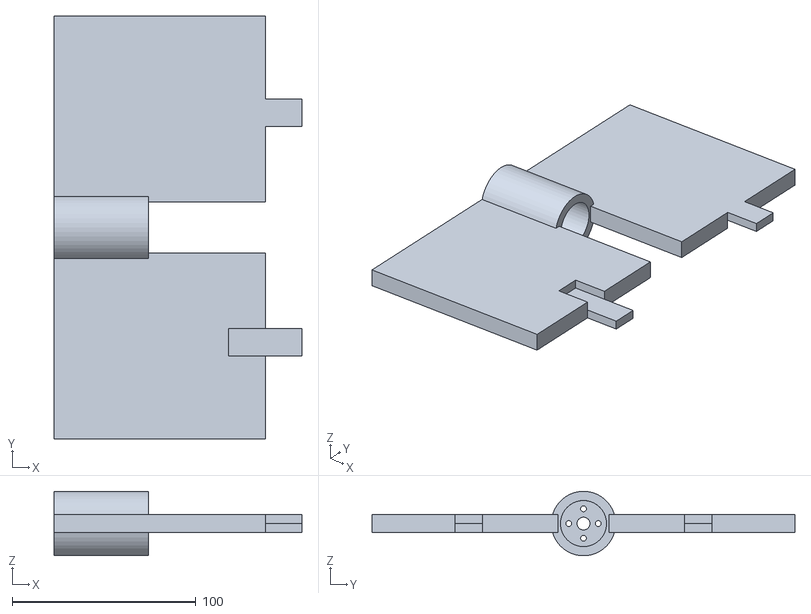
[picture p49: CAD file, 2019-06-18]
hardware/v2/wheel_support.stl
135.0 x 230.0 x 35.1

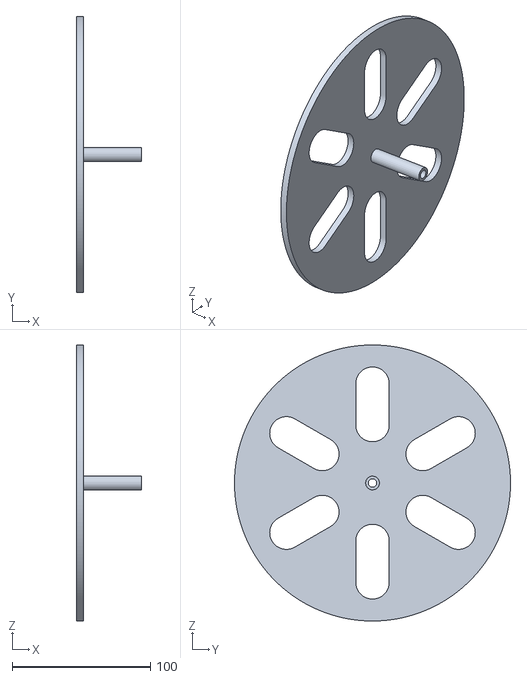
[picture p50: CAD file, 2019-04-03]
hardware/v2/right_wheel.stl
47.0 x 200.0 x 200.0

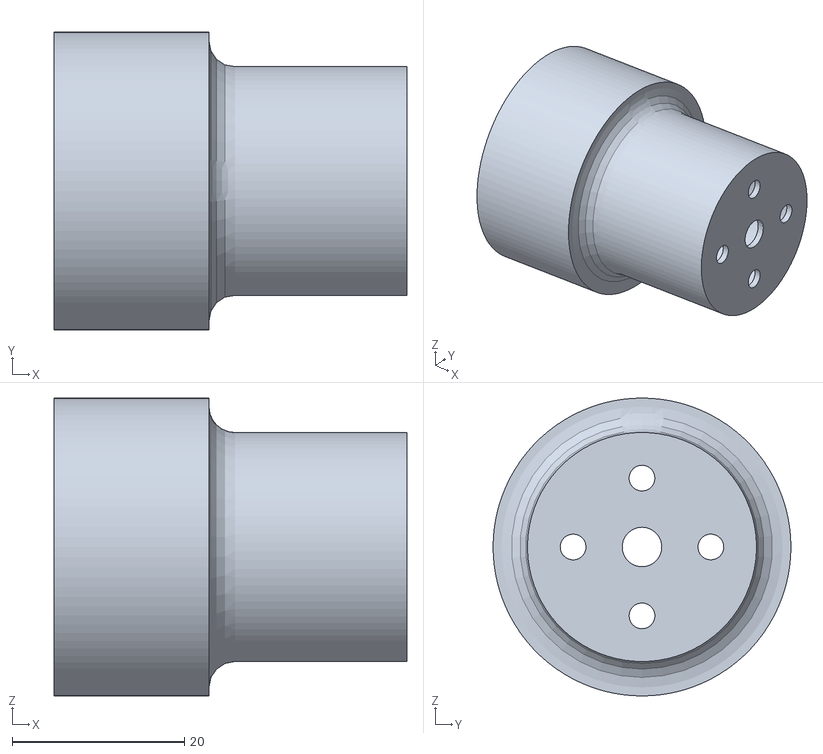
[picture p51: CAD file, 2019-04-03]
hardware/v2/motor_support.stl
41.0 x 34.6 x 34.6

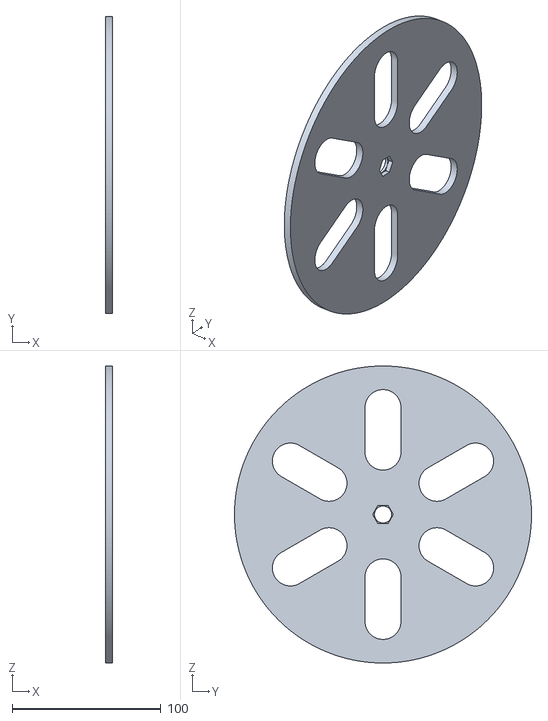
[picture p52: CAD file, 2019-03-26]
hardware/v2/left_wheel.stl
5.00 x 200.0 x 200.0

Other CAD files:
hardware/v2/reinforcements.FCStd
hardware/v2/big_wheel.stl
hardware/v2/U_support.stl

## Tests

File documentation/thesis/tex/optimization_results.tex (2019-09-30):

\section{Optimization Results} \label{sec: parameters results}
This section tries to find the optimal parameters given the equation that relate these parameters with the cost
and the restriction defined before.

Our procedure has been making a grid with the four parameters of the robot 
design: $w$ (width of the cylinders), $N$(number of cylinders), $r_{wheel}$ and $r_{flywheel}$.
We have fixed $r_{flywheel}$ to a number of discrete values between 0.05 and 0.125 and, for each one, we evaluate the cost for each point of the grid,
remove those which do not fulfill the restrictions, and keep the configuration providing the minimum cost. 

\begin{figure}[H]
	\centering
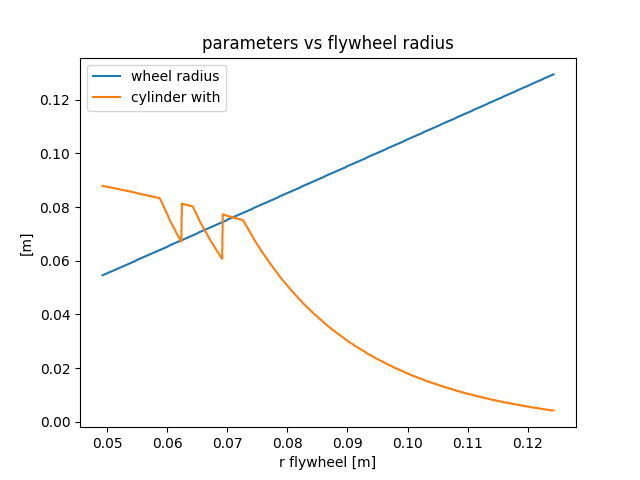
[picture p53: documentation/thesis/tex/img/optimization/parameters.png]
	
	\caption{Plot of the wheel radius and the width of the cylinder that was optimal for each flywheel radius.}
	\label{fig:Parameters plot}
\end{figure}

We can observe that the relation between the flywheel radius and 
the wheel radius is linear. This is because we are always on the
edge of the restriction number one.

\begin{figure}[H]
	\centering
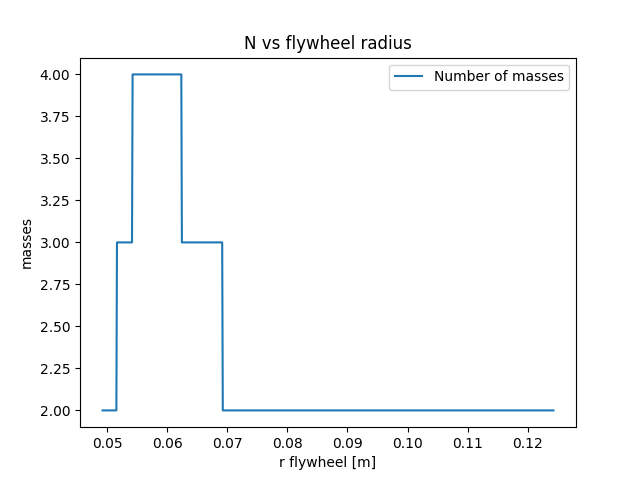
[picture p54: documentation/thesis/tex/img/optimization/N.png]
	
	\caption{Plot of the N that minimize the cost function.}
	\label{fig:Parameters plot}
\end{figure}

\begin{figure}[H]
	\centering
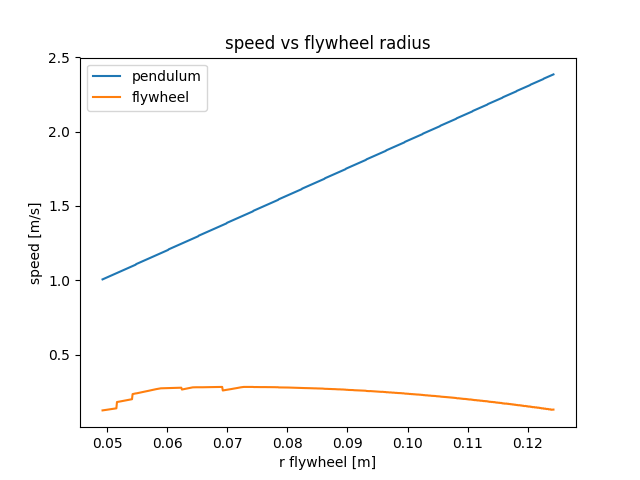
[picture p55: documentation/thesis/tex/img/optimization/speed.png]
	
	\caption{Plot of the equations \ref{Maximum speed flywheel} and \ref{maximum speed pendulum} at the parameters that minimize the cost function and fullfil the requirements and restrictions}
	\label{fig:Speed plot}
\end{figure}

In this figure we can observe that the speed of in the pendulum mode increases
linearly with the flywheel radius. This is because it is linearly related with
the wheel radius.

\begin{figure}[H]
	\centering
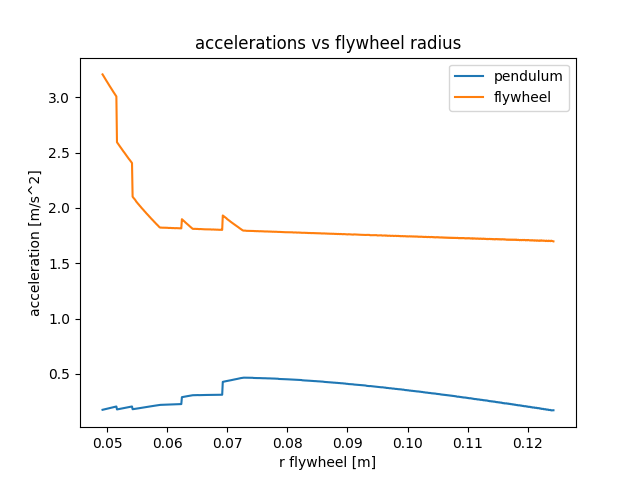
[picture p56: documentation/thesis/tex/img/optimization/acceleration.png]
	
	\caption{Plot of the equations \ref{maximum acceleration flywheel} and \ref{maximum acceleration pendulum} at the parameters that minimize the cost and fulfill the requirements and restrictions}
	\label{fig:Speed plot}
\end{figure}

\begin{figure}[H]
	\centering
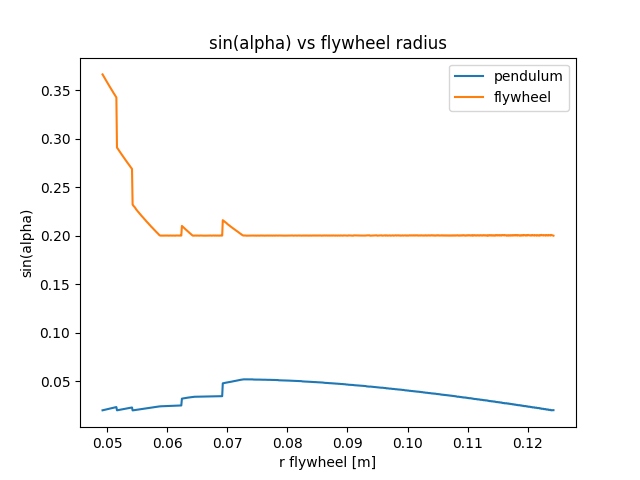
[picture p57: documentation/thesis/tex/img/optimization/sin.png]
	
	\caption{Plot of the equations \ref{Maximum angle using flywheel system} and \ref{Maximum angle using pendulum system} at the parameters that minimize the cost and fulfill the requirements and restrictions}
	\label{fig:Sinus plot}
\end{figure}

We can see in figure \ref{fig:Sinus plot} that when the flywheel radius 
exceeds 0.07 m the requirement of the flywheel sinus becomes active.

\begin{figure}[H]
	\centering
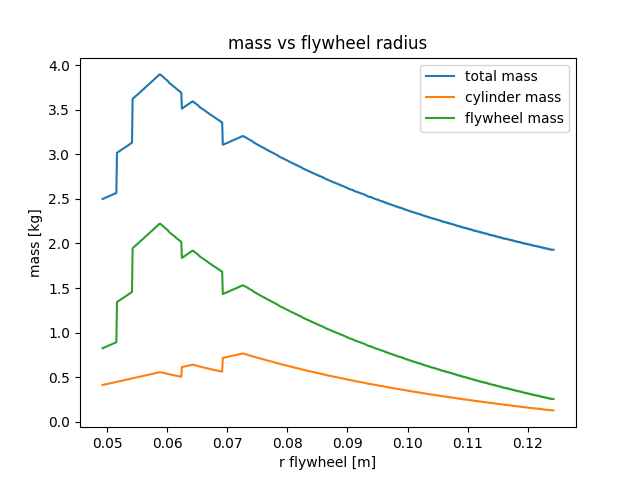
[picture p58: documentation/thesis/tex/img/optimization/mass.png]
	
	\caption{Plot of the mass for each configuration.}
	\label{fig:Mass plot}
\end{figure}

We can see in figure \ref{fig:Mass plot} that the total mass never exceeds the
5 kg limit.

%\begin{figure}[H]
%	\centering
%	\includegraphics[width=10cm]{img/optimization/height.png}
%	\caption{Plot of the equation \ref{Maximum height} for each configuration.}
%	\label{fig:Mass plot}
%\end{figure}

\begin{figure}[H]
	\centering
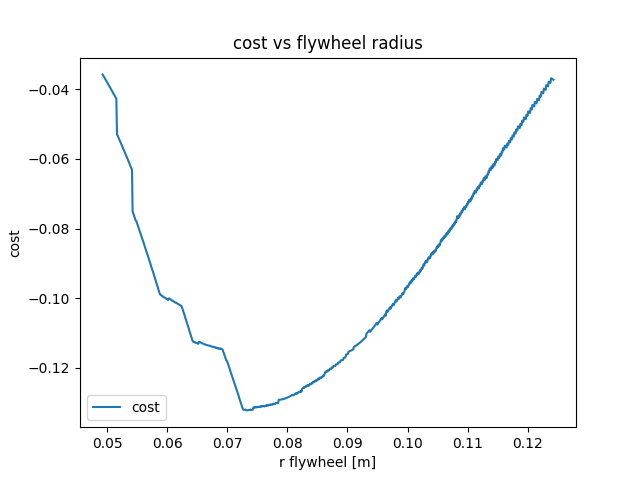
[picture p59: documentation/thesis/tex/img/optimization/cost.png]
	
	\caption{Plot of the equation \ref{eq: cost} for each configuration.}
	\label{fig:Cost plot}
\end{figure}

Seeing the parameters that minimize cost and the material that we had available
our selected parameters were:
\begin{center}
	\begin{tabular}{ |c|c|c|c| } 
	 \hline
	 $r_{flywheel}$ & $r_{wheel}$ & $w$ & $N$\\
	 \hline 
	 8cm & 10cm & 5cm & 2 \\ 
	 \hline
	\end{tabular}
\end{center}

With these parameters we get the following specifications:
\begin{center}
	\begin{tabular}{ |c|c| } 
	 \hline
	 Total mass & 2,91 kg\\
	 \hline
	 \textbf{Pendulum} \\
	 \hline
	 Maximum sinus & 0,042\\
	 \hline
	 Maximum speed horizontal & 1,84 $m/s$\\
	 \hline
	 Maximum acceleration horizontal & 0,38 $m/s^2$\\
	 \hline
	 \textbf{Flywheel} \\
	 \hline
	 Maximum sinus & 0,171\\
	 \hline
	 Maximum speed horizontal & 0,24 $m/s$\\
	 \hline
	 Maximum acceleration horizontal & 1.52 $m/s^2$\\
	 \hline
	\end{tabular}
\end{center}

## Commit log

2018-11-08 first iteration design
    [Rough Pi Model.stl, robot.fcstd]
2018-11-08 added battery and holes
    [robot.fcstd]
2018-11-14 centered batteries
    [robot.fcstd]
2018-11-21 peca amb forats
    [robot.fcstd]
2018-11-26 fleewheel in two
    [half_fleewheel.stl, robot.fcstd]
2018-11-28 left_fly wheel
    [left_fly_wheel.stl, robot.fcstd]
2018-11-28 right fly wheel
    [half_fleewheel.stl, right_fly_wheel.stl, robot.fcstd]
2018-12-13 first version of the thesis
    [robot.fcstd]
2018-12-17 Pendulum case
2019-01-29 Mech results
    [robot.fcstd]
2019-02-24 added sockets to planner and components
2019-02-24 socket first exchange
2019-02-24 socket reference send to controller
2019-03-05 wheel force diagram
2019-03-26 hardware v2
    [left_wheel.stl, right_wheel.stl, robot.fcstd]
2019-03-26 holes for baterrys
    [robot.fcstd]
2019-03-27 more tight and placing the holes well
    [robot.fcstd]
2019-03-28 corrected motor syupport
    [motor_support.stl, robot.fcstd]
2019-03-28 corrected motor holes
    [robot.fcstd]
2019-04-01 right wheel varilla
    [right_wheel.stl, robot.fcstd]
2019-04-04 central body
    [central_body.stl, robot.fcstd]
2019-04-14 added height and external torque
2019-05-19 renamig wheel data
2019-05-30 Pin names
2019-05-31 user interface
    [circuit.kicad_pcb, circuit.sch]
2019-06-03 Aplying pwm
2019-06-14 single motor
    [hardware_config_single_motor.json]
2019-06-14 Single motor socket
    [hardware_config_simple_motor.json]
2019-06-14 Speed conection
    [hardware_config_simple_motor.json]
2019-06-15 Changed direction method
    [hardware_config_simple_motor.json]
2019-06-15 Motor with encoder
    [hardware_config_motor.json]
2019-06-15 mispell encoder
    [hardware_config_motor.json]
2019-06-15 Motor loop state
2019-06-16 PID debug
2019-06-16 encoder flags
2019-06-16 debuging encoder
    [hardware_config_motor.json]
2019-06-16 going to interrupts
2019-06-16 only one interrupt
    [hardware_config_motor.json]
2019-06-16 glitch filter
2019-06-16 glithc filter
2019-06-16 PWM reference
2019-06-16 PWM frequency
2019-06-16 PWM freq
2019-06-16 filtering speed
    [hardware_config_motor.json]
2019-06-16 PID parameters
    [hardware_config_motor.json]
2019-06-16 change PID parameters
    [hardware_config_motor.json]
2019-06-16 PID parameter
    [hardware_config_motor.json]
2019-06-16 minus i
    [hardware_config_motor.json]
2019-06-17 sensor read
2019-06-18 llenguetes central body
    [central_body.stl, robot.fcstd]
2019-06-18 wheel support
    [robot.fcstd, wheel_support.stl]
2019-06-18 mes patiles, gruix aguanta rodament
    [central_body.stl, robot.fcstd]
2019-06-18 changed hardware config
    [hardware_config_motor.json]
2019-06-19 Kp to 0.5
    [hardware_config_motor.json]
2019-06-19 kp 0.1
    [hardware_config_motor.json]
2019-06-19 Kp 0.01
    [hardware_config_motor.json]
2019-06-19 lateral body
    [lateral_body.stl, robot.fcstd]
2019-06-21 big wheel
    [big_wheel.stl, robot.fcstd]
2019-06-21 PWM limit
    [hardware_config_motor.json]
2019-06-21 PWM limit 0.6
2019-06-21 PWM 1
2019-06-26 wheel data graph
2019-06-27 big wheel exterior
    [big_wheel_exterior.stl, robot.fcstd]
2019-06-27 updated server ip
    [hardware_config_motor.json]
2019-07-02 free cylinder
2019-07-04 minimum torque set to 0
2019-07-09 planner sockets
2019-07-09 new pinout
    [hardware_config_motor.json]
2019-07-09 three motors
2019-07-31 motor log rate
2019-08-01 PWM instead of output
2019-08-01 motor for component
2019-09-12 is motor stopped?
2019-09-13 change stabilizer filter
2019-09-26 bearings capture
